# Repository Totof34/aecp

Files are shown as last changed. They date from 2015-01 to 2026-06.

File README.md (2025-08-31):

aecp
====

The project describes a electronic mapped car ignition
especialy for Panhard two cylindre

If you would have more information about this project please visit 
www.audiyofan.org

A link to the dedicated post 
http://www.audiyofan.org/forum/viewtopic.php?f=71&t=9221

PCB & schema are designed with Kicad

**********************************
*A new version called V4 in 2025*
**********************************

The new board in 2025

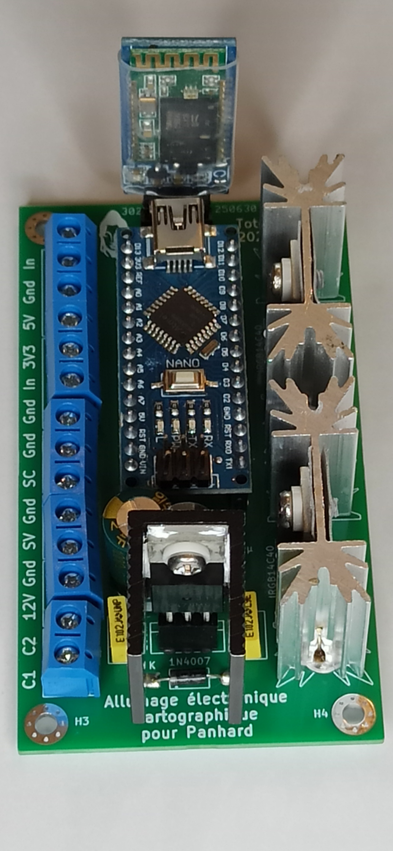
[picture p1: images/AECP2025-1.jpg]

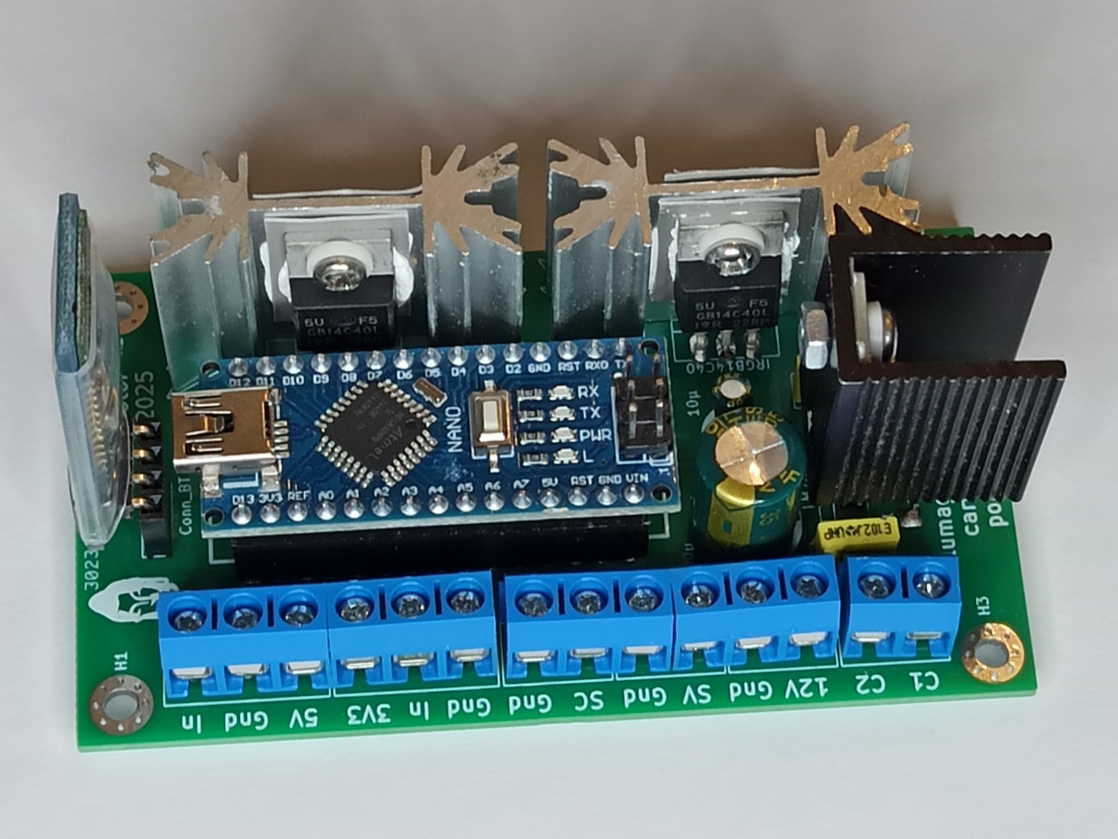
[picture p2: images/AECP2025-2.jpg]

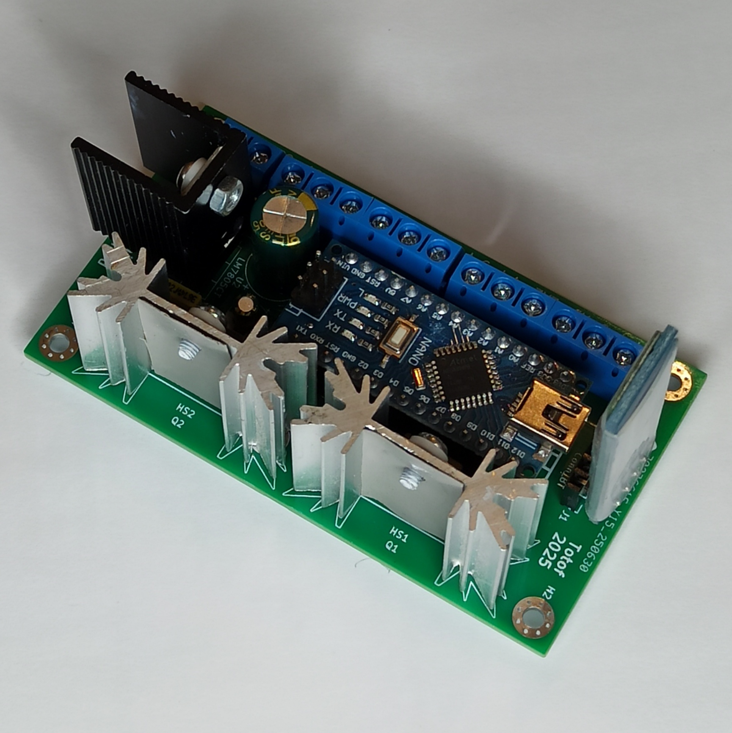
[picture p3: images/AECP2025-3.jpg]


For the Gerber's file see the folder "aecp/source_kicad/gerber V4/"

all PCB Gerber files and 3D printing files from version 2025 grouped in the folder "aecp/manufacturing_files"

*******************************************************************

the new board uses a Atmega328 and usb link or a bluetooth module ( HC-05 or 06 )
to transmit some data to the PC

it's a Arduino Nano_V3

The idea comes from this site
http://a110a.free.fr/SPIP172/plan.php3

with this startpoint
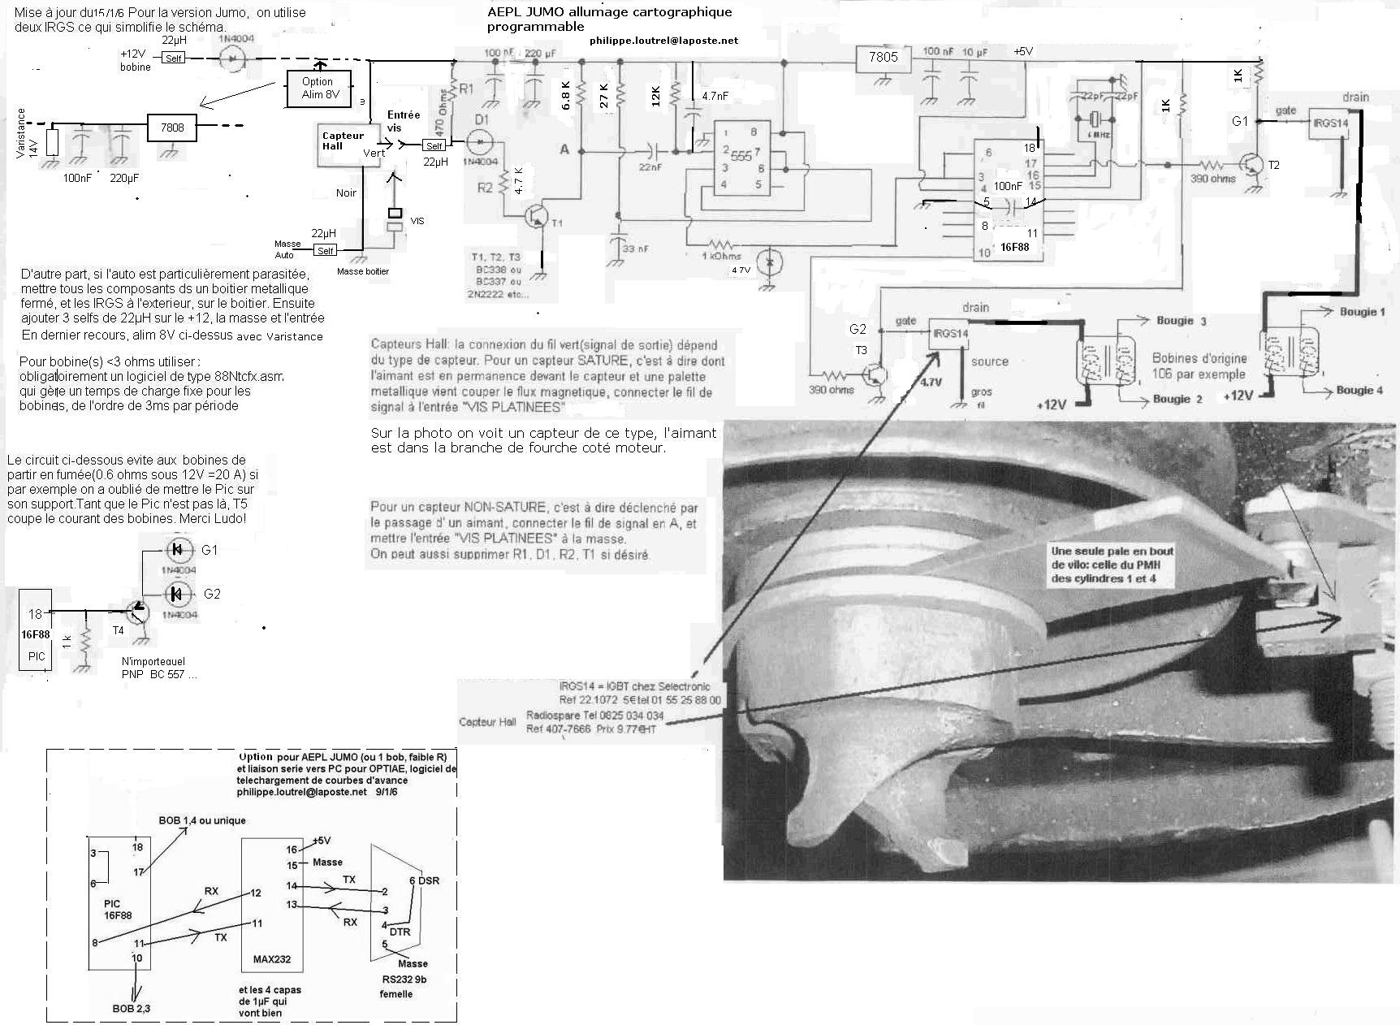
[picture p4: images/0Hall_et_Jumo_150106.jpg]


And finally with a Nano V3.0 with a dedicated page here
http://a110a.free.fr/SPIP172/article.php3?id_article=142

But this project have some child too for exemple 
https://github.com/michelm63/AEMM
with a dedicated post here
http://motos-anglaises.com/phpBB3/viewtopic.php?f=3&t=28953

All the things we need is on this picture for the hardware,
and a car of course to use it !!
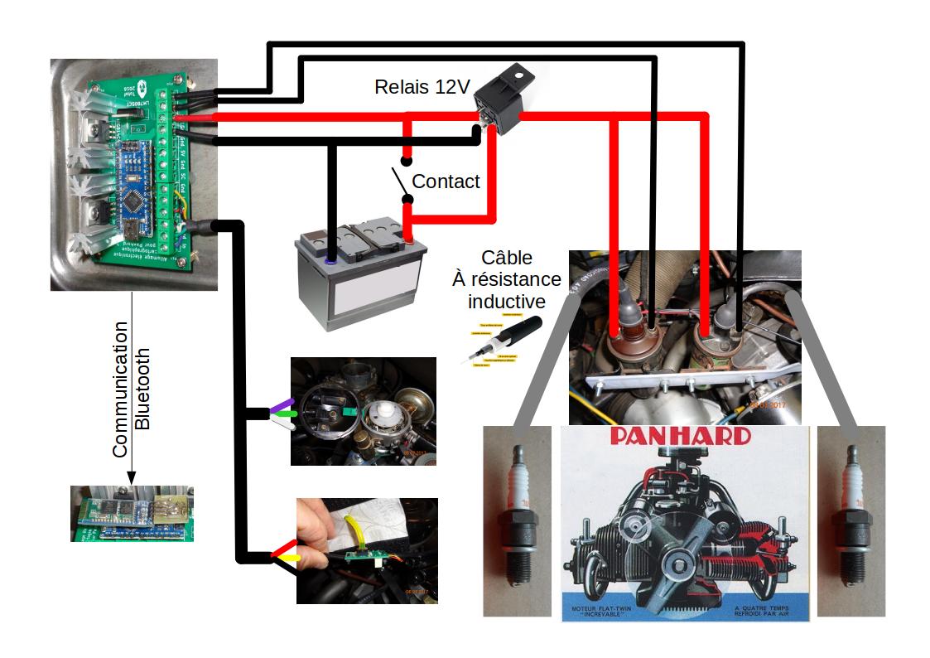
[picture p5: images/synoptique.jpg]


The prototype of the new board under construction and under kicad

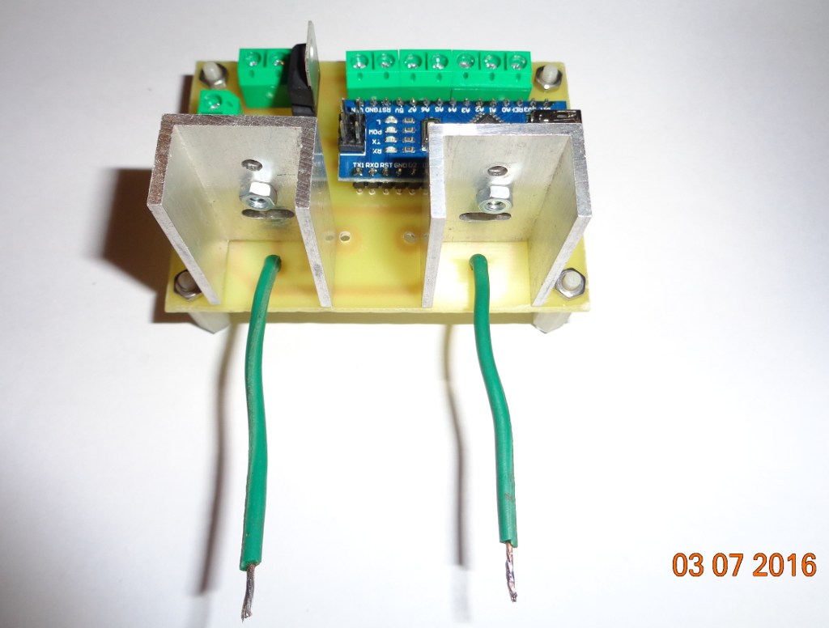
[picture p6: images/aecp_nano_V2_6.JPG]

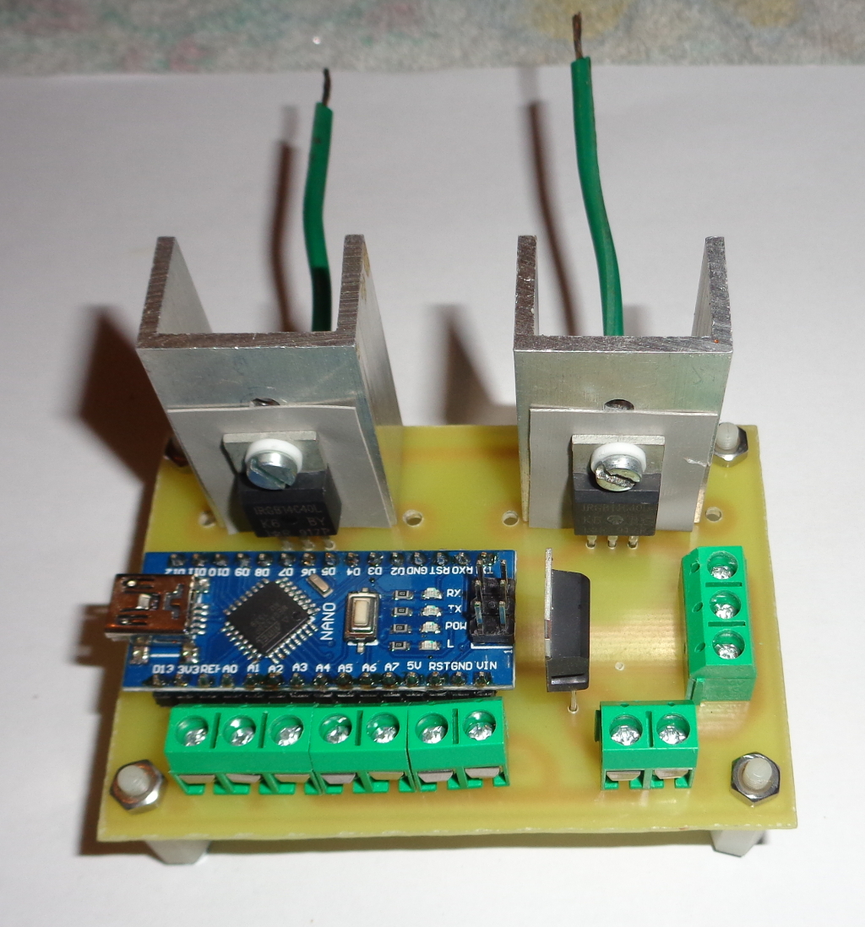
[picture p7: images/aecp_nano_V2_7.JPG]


With some parts 

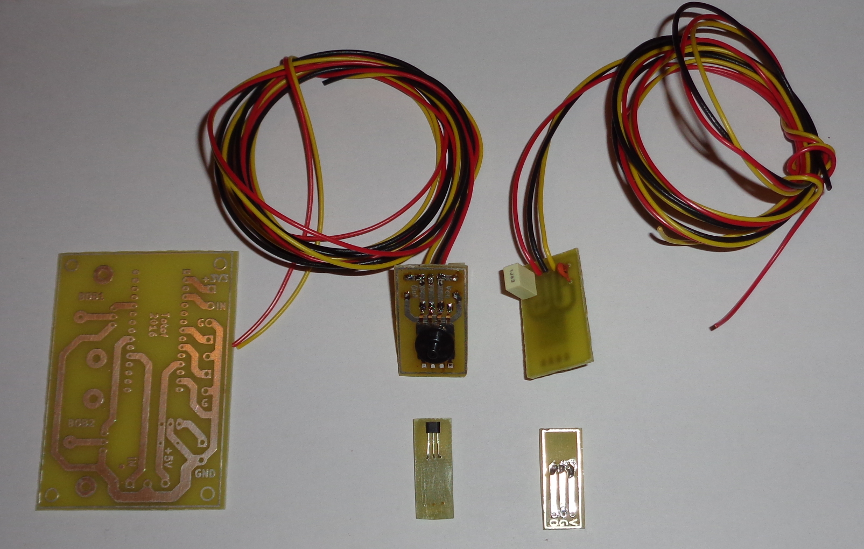
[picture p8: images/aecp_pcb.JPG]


The new version of the PCB for longtime test

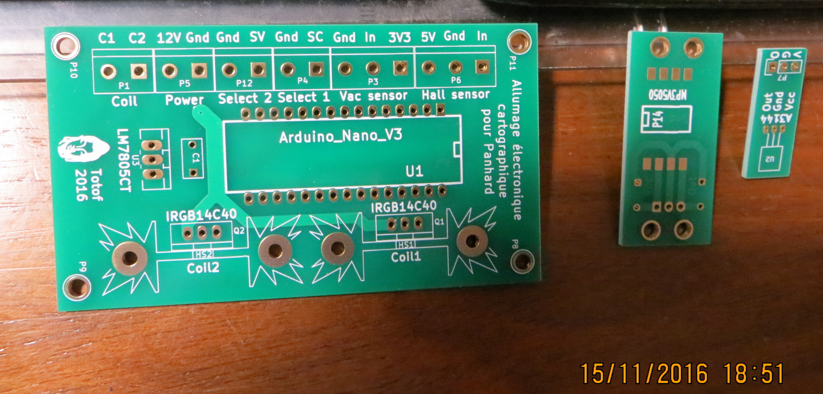
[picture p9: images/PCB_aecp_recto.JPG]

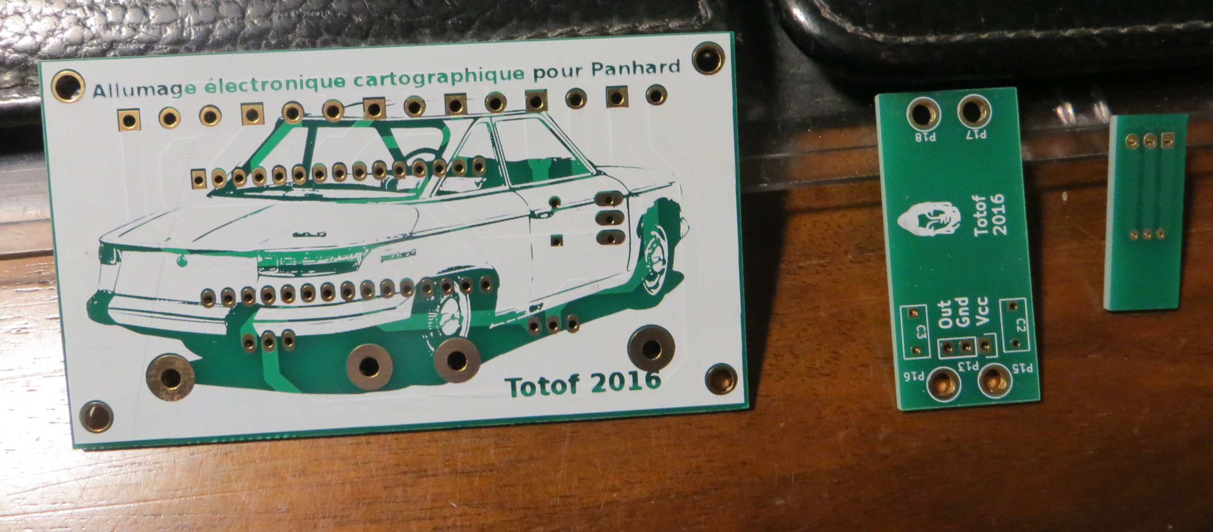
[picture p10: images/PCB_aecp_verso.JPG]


You can select different curve with a box

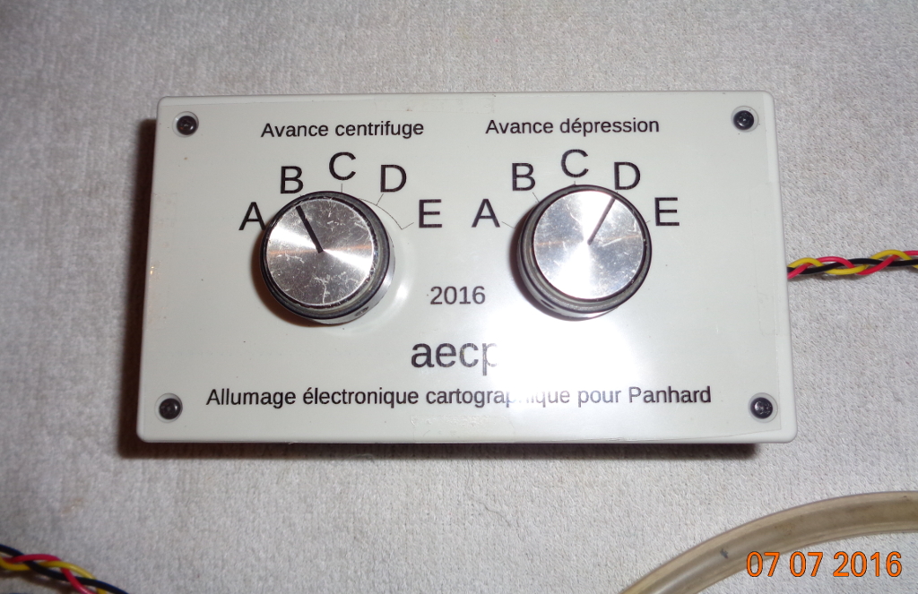
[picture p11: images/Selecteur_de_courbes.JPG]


To develop our electronic ignition, we create an new interface with a Nano_V3
to receive data from the Atmega328 and visualize the centrifugal advance curves and vacuum advance

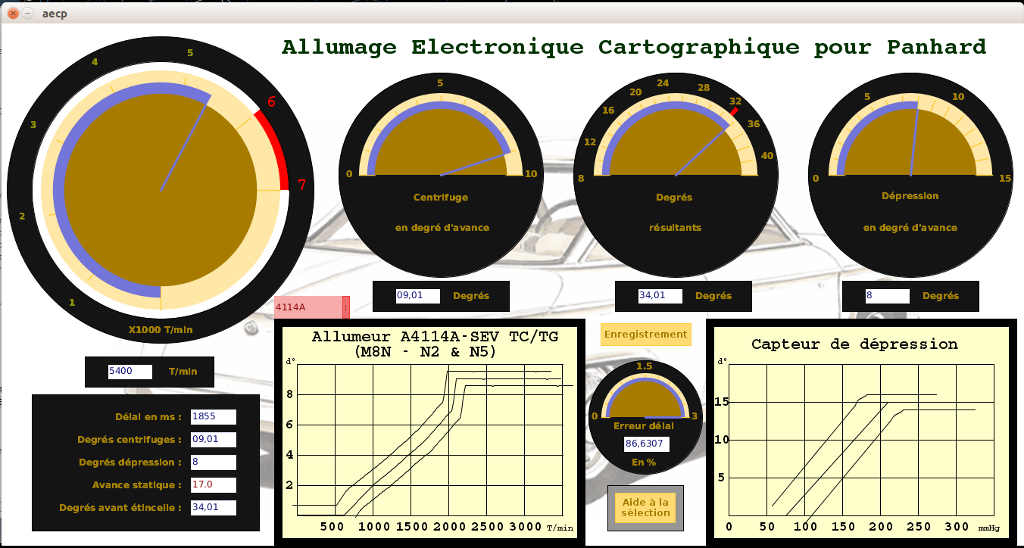
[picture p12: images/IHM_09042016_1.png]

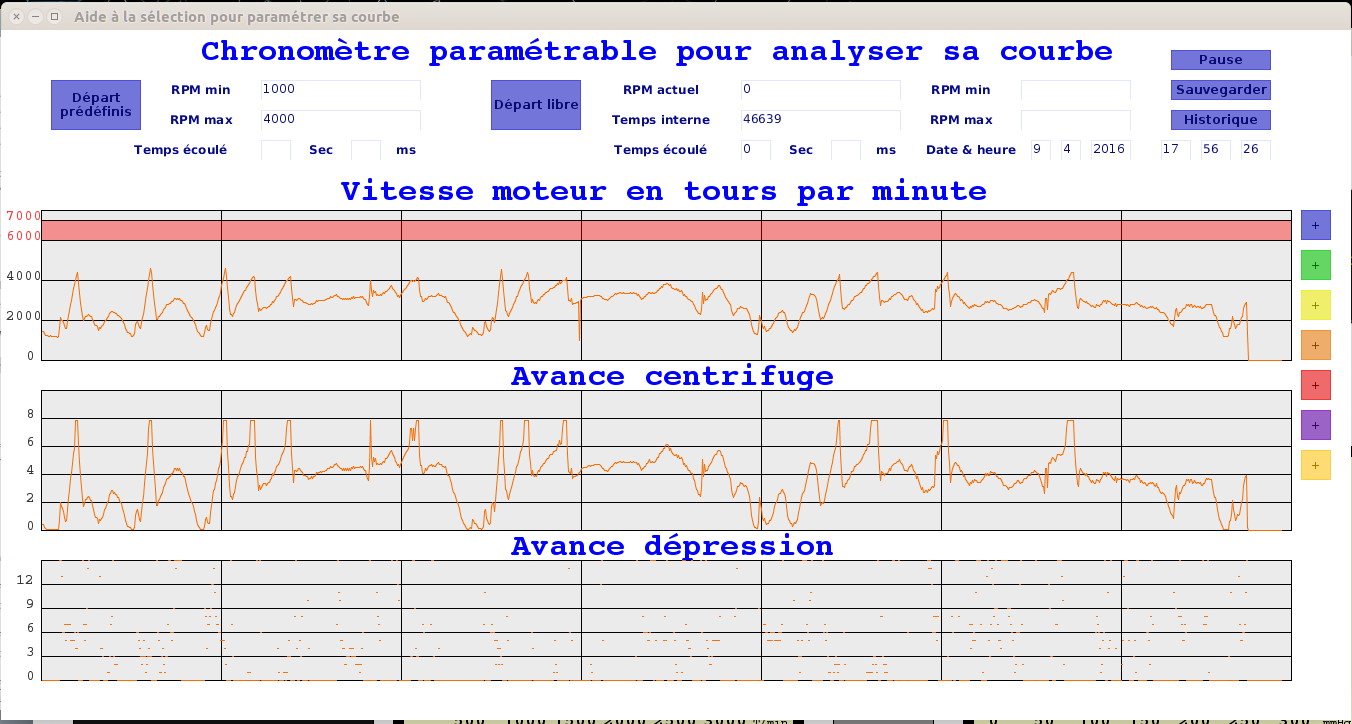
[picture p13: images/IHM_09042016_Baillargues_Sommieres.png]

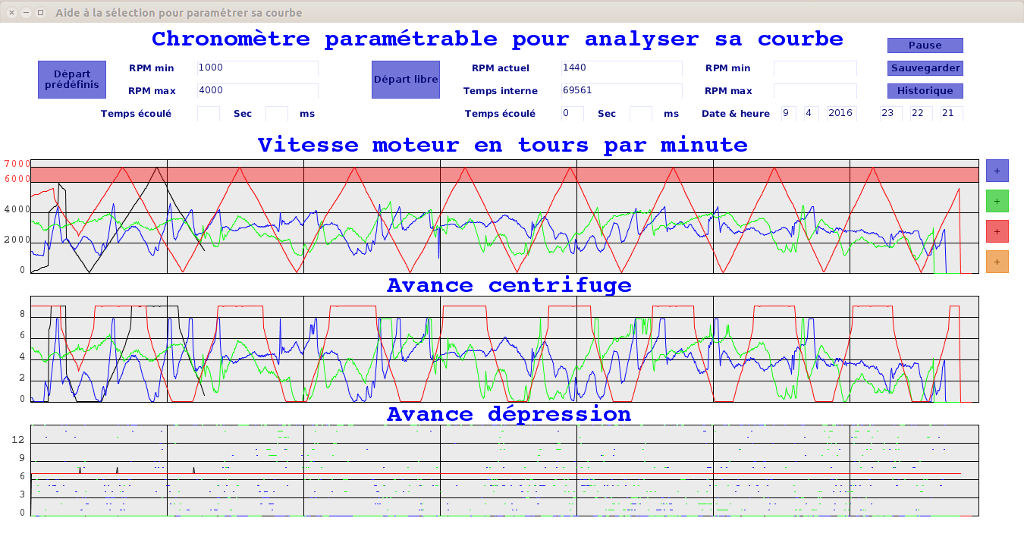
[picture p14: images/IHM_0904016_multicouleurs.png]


This interface is designed under Processing IDE and the board is programmed with Arduino IDE
All the files available in subfolders

For the printed circuit board please see the source_kicad folder 
or the build folder for a made version

For the schema see below

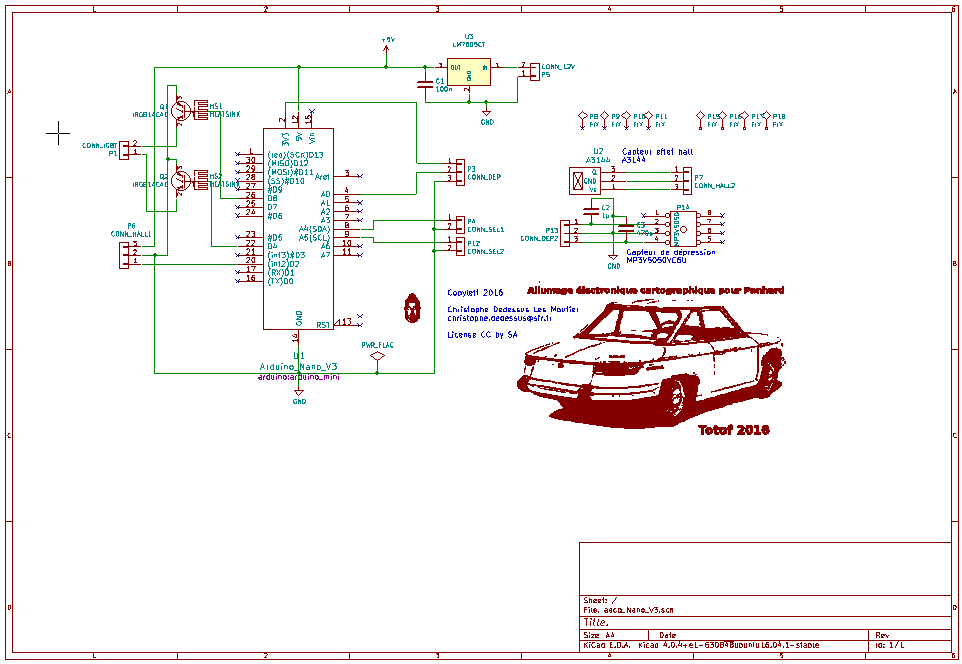
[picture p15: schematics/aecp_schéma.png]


for the rest, I suggest you to navigate into folders and open the pdf

The main code is explained through comments ( in French) in the ino file ( see Arduino folder )

Enjoy

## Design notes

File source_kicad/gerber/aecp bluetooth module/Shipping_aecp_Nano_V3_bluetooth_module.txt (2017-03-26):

aecp_Nano_V3_bluetooth_module - 26/03/2017 

Amount of Layers  : 2
PCB Thickness     : 1.6 mm
Copper Thickness  : 35 um
Plating           : Enig
Solder Mask Color : Green
Silkscreen        : Double Side
PCB Technology    : No SMD
Peel Off          : No
Electric Test     : No
Production Time   : Standard
Delivery Form     : Single PCB
PCB Dimension X   : 43.00 mm
PCB Dimension Y   : 20.00 mm
Quantity          : 20
Price per Piece   : x.xx €
Subtotal          : x.xx €

Country           : France
Shipping Method   : Registered Airmail
Payment Method    : PayPal

Votre adresse
Votre adresse
Votre adresse
Votre adresse

Phone    : +33 
Username :  
mail     :

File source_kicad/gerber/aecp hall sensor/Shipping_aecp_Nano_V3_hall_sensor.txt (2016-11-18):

aecp_Nano_V3_hall_sensor - 05/11/2016 

Amount of Layers  : 2
PCB Thickness     : 1.6 mm
Copper Thickness  : 35 um
Plating           : Enig
Solder Mask Color : Green
Silkscreen        : Double Side
PCB Technology    : No SMD
Peel Off          : No
Electric Test     : No
Production Time   : Standard
Delivery Form     : Single PCB
PCB Dimension X   : 28.00 mm
PCB Dimension Y   : 10.00 mm
Quantity          : 20
Price per Piece   : x.xx €
Subtotal          : x.xx €

Country           : France
Shipping Method   : Registered Airmail
Payment Method    : PayPal

Mr Chanteperdrix Roger
7 impasse les pêchers
34670 Baillargues
France

Phone    : +334.67.87.15.21
Username :  
mail     : chanteperdrix34@gmail.com

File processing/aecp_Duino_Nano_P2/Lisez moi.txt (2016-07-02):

Bonjour 

Cette interface peut fonctionner sous Linux mais aussi windows ou mac 
pour cela il faut adapter quelques lignes de code ou entrée dans certain fichier

La version de Processing est 2.2.1 , une migration vers Processing 3 sera possible
ultérieurement

Commencer par vérifier que vous aillez les bonne librairies d'installées ainsi que les outils
Pour la librairie c'est G4P de peter Lager 
Pour l'outil c'est G4P GUI builder de peter Lager

Ensuite il faut adapter à son OS le fichier aecp.conf
Sous Linux (comme sous mac)les chemins sont du type ci-dessous
aefmespath /home/monuser/sketchbook/myproject/aecp_Duino_Nano/aef/
AEFpath /home/monuser/sketchbook/myproject/aepl_Duino_Nano_V2/aef/PL17_pierre_baillargues_sommières.aef

Sous Windows les chemins deviennent
aefmespath C:\Users\monuser\Documents\sketchbook\myproject\aecp_Duino_Nano\aef\
AEFpath C:\Users\monuser\Documents\sketchbook\myproject\aecp_Duino_Nano\aef\mondernierfichierouvert.aef

Ce qui va aider a la fluidité d'enregistrement et recharge de l'historique ;-)

Autre différence entre linux et windows pour l'enregistrement des "data" 
il faut modifier le fichier plotutil.pde
Sous linux la fonction recordall() s'écrit comme ci-dessous
public void recordall(){
  sExportdata = ( sName + " " + day + " " + month + " " + year + " " + hour + " " + minute + " " + second);
  sData[0] = sExportdata;
  sExportdata = (speedValue + " " + correcteddelayDegree + " " + pressionValue +"\r"); // Attention version windows, enlever le "\r" car génère un CLRF
  sData[xrpmPos] = sExportdata;
  //println(sExportdata);
  //println(xrpmPos);
  //saveStrings(sName + ".aef", sData);
}
Sous windows on n'a pas besoin du caractère de fin de ligne "\r" et donc la fonction recordall() devient
public void recordall(){
  sExportdata = ( sName + " " + day + " " + month + " " + year + " " + hour + " " + minute + " " + second);
  sData[0] = sExportdata;
  sExportdata = (speedValue + " " + correcteddelayDegree + " " + pressionValue); // Attention version windows, enlever le "\r" car génère un CLRF
  sData[xrpmPos] = sExportdata;
  //println(sExportdata);
  //println(xrpmPos);
  //saveStrings(sName + ".aef", sData);
}

Je compléterai au gré des problèmes rencontrés, mon mail pour toutes questions si besoin
christophe.dedessus@sfr.fr

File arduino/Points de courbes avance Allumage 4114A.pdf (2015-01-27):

## Points de courbe "AVANCE CENTRIFUGE"

## pour Moteur M8N

Nbr de Tours Allumeur | Avance en DEGRE
550 | 0
1700 | 5
1800 | 5,5
1900 | 6,1
2000 | 6,8
2020 | 6,9
2040 | 7,1
2060 | 7,3
2080 | 7,55
2090 | 7,9
3000 | 7,9
3500 | 7,9

# Points de courbe "AVANCE DEPRESSION"

# pour Moteur M8N

Dépression en mm Hg | Avance en DEGRE
78 | 0
190 | 13,5
192 | 13,8
194 | 14,1
196 | 14,3
198 | 14,4
200 | 14,5
202 | 14,6
204 | 14,75
206 | 14,90
208 | 15,0
300 | 15,0
320 | 15,0

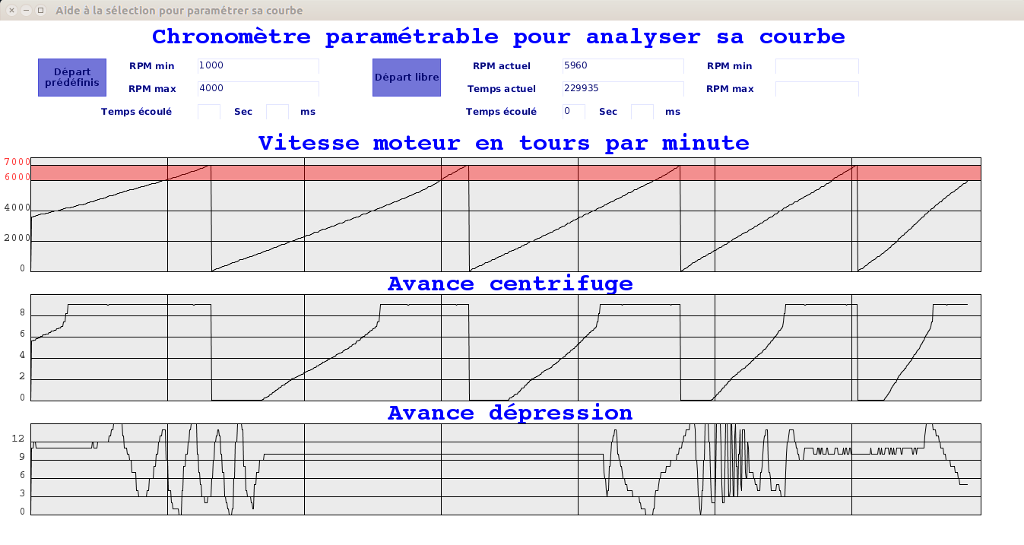
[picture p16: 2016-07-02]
images/aecp_02042016_w3.png

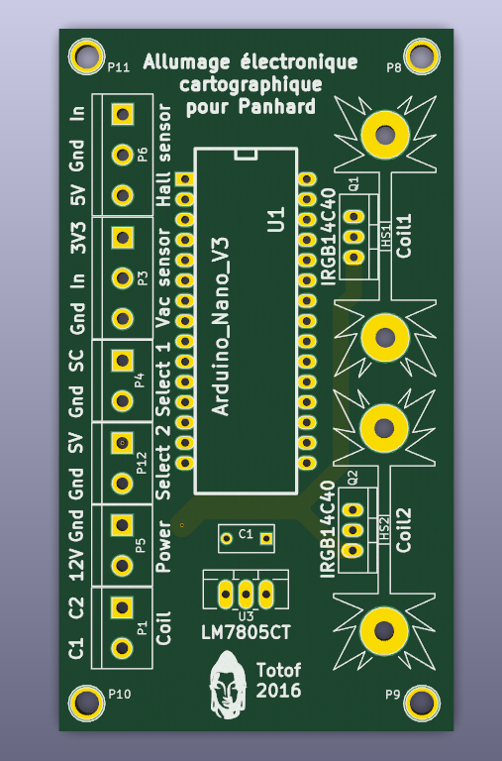
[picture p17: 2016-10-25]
images/aecp_Nano_V3_3D1.png

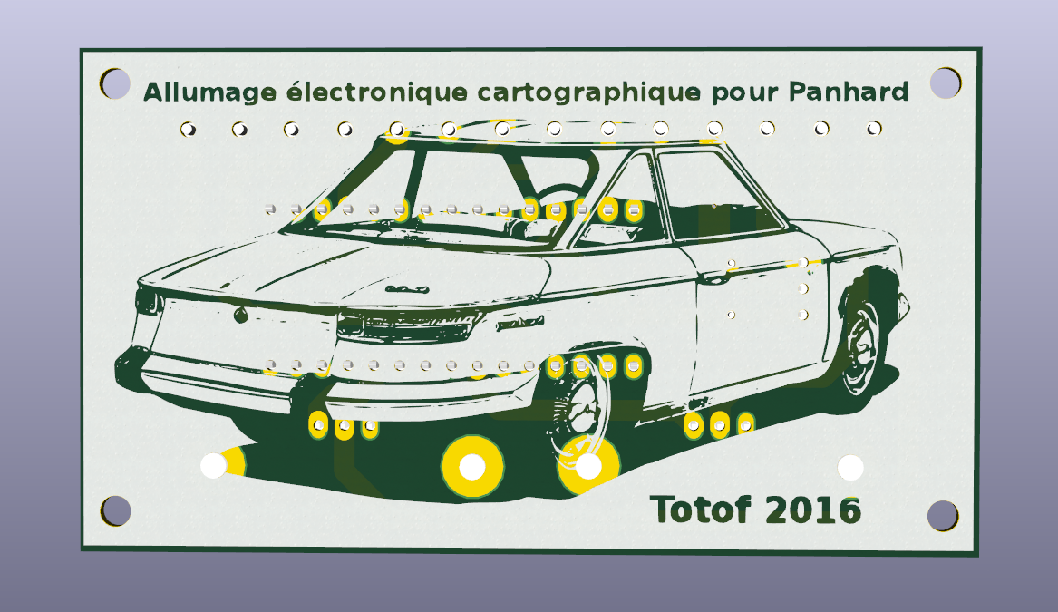
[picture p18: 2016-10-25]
images/aecp_Nano_V3_3D3.png

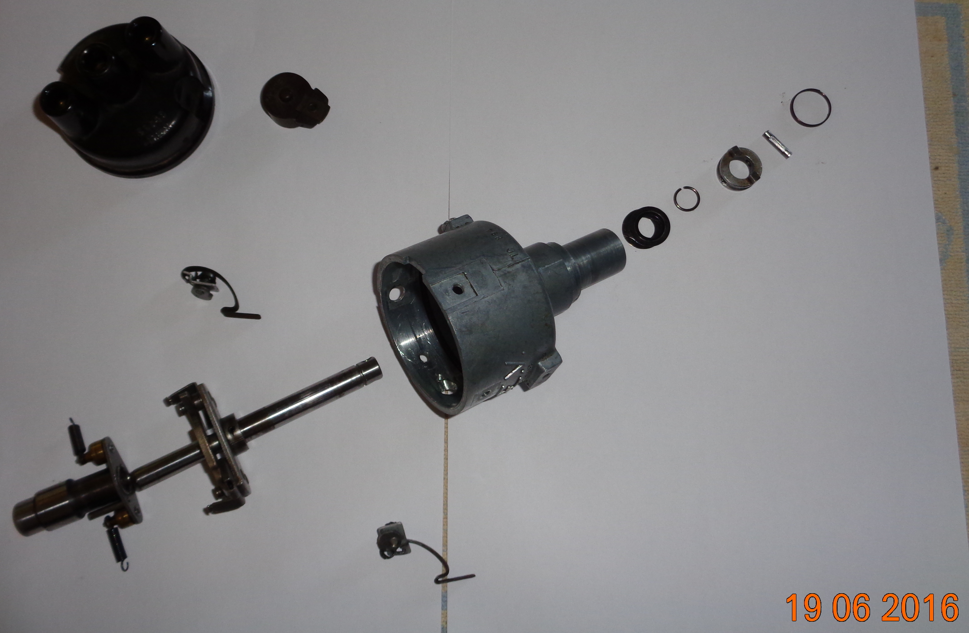
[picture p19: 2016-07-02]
images/Allumeur en pieces.JPG

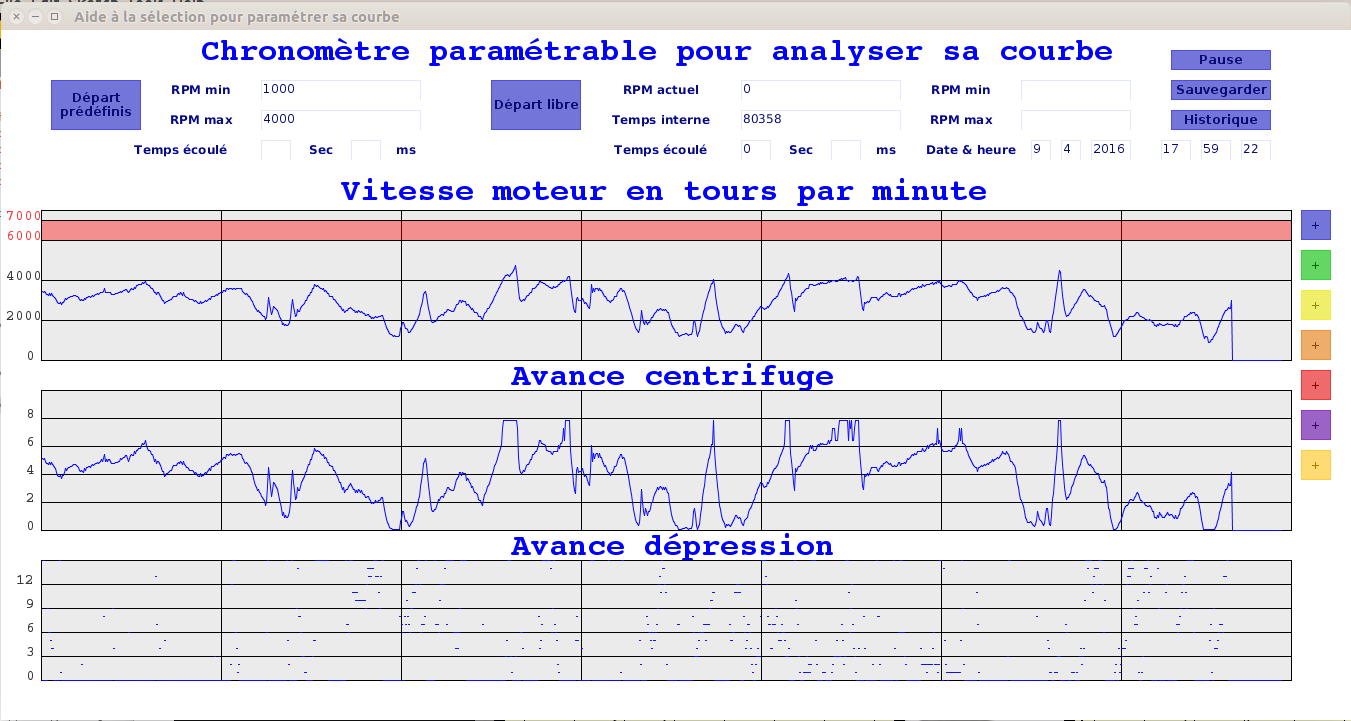
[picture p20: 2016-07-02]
images/IHM_09042106_Sommieres_Saint Drézéry.png

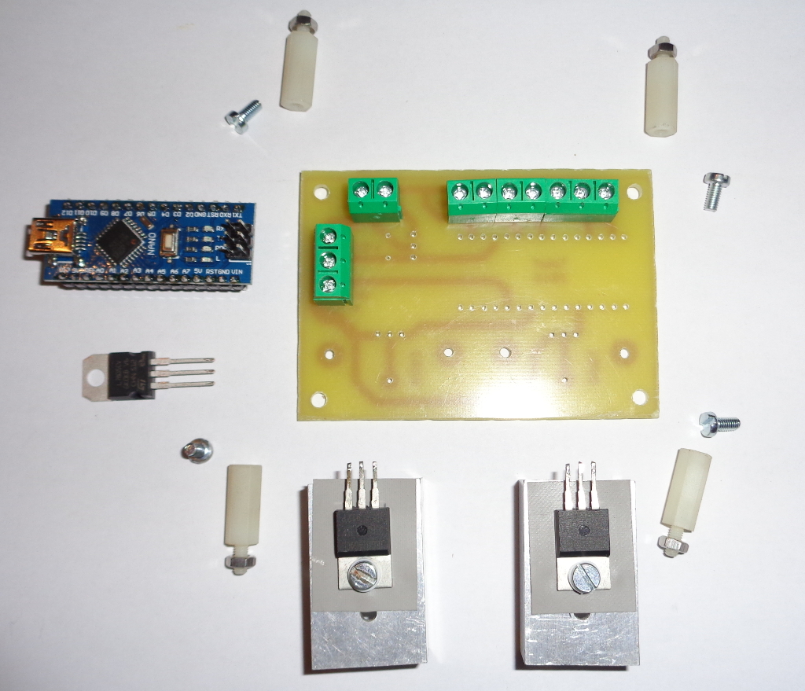
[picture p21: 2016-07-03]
images/aecp_nano_V2_3.JPG

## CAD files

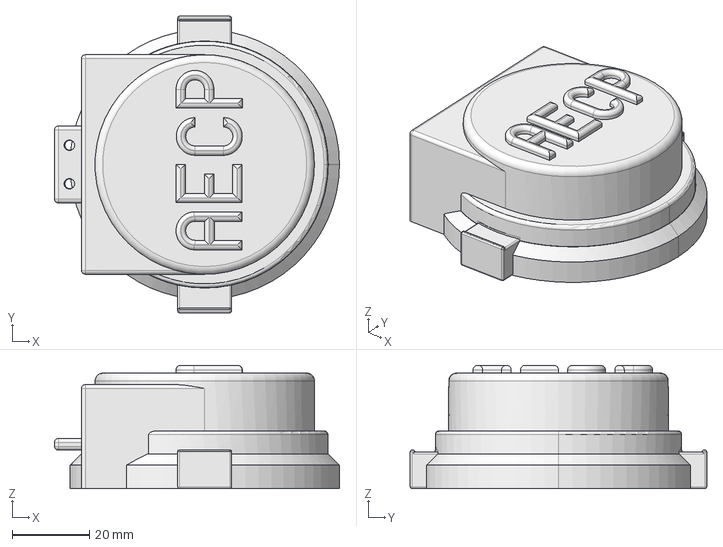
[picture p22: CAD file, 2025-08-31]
manufacturing_files/Tete delco AECP.step
74.0 x 77.0 x 32.0 mm

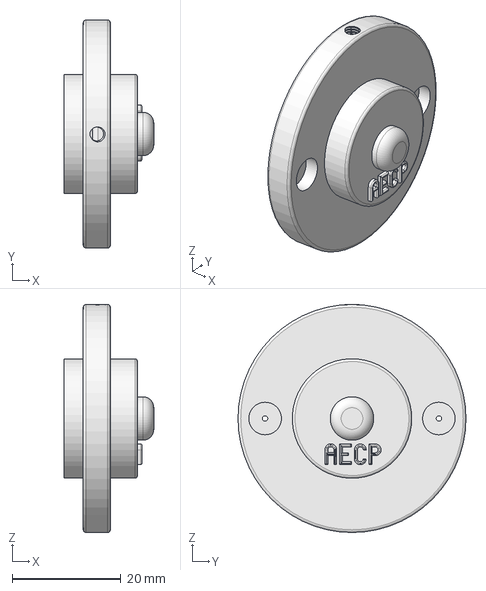
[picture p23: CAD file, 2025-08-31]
manufacturing_files/Doigt AECP.step
16.5 x 42.0 x 42.0 mm

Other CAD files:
manufacturing_files/Tete delco AECP V2.step

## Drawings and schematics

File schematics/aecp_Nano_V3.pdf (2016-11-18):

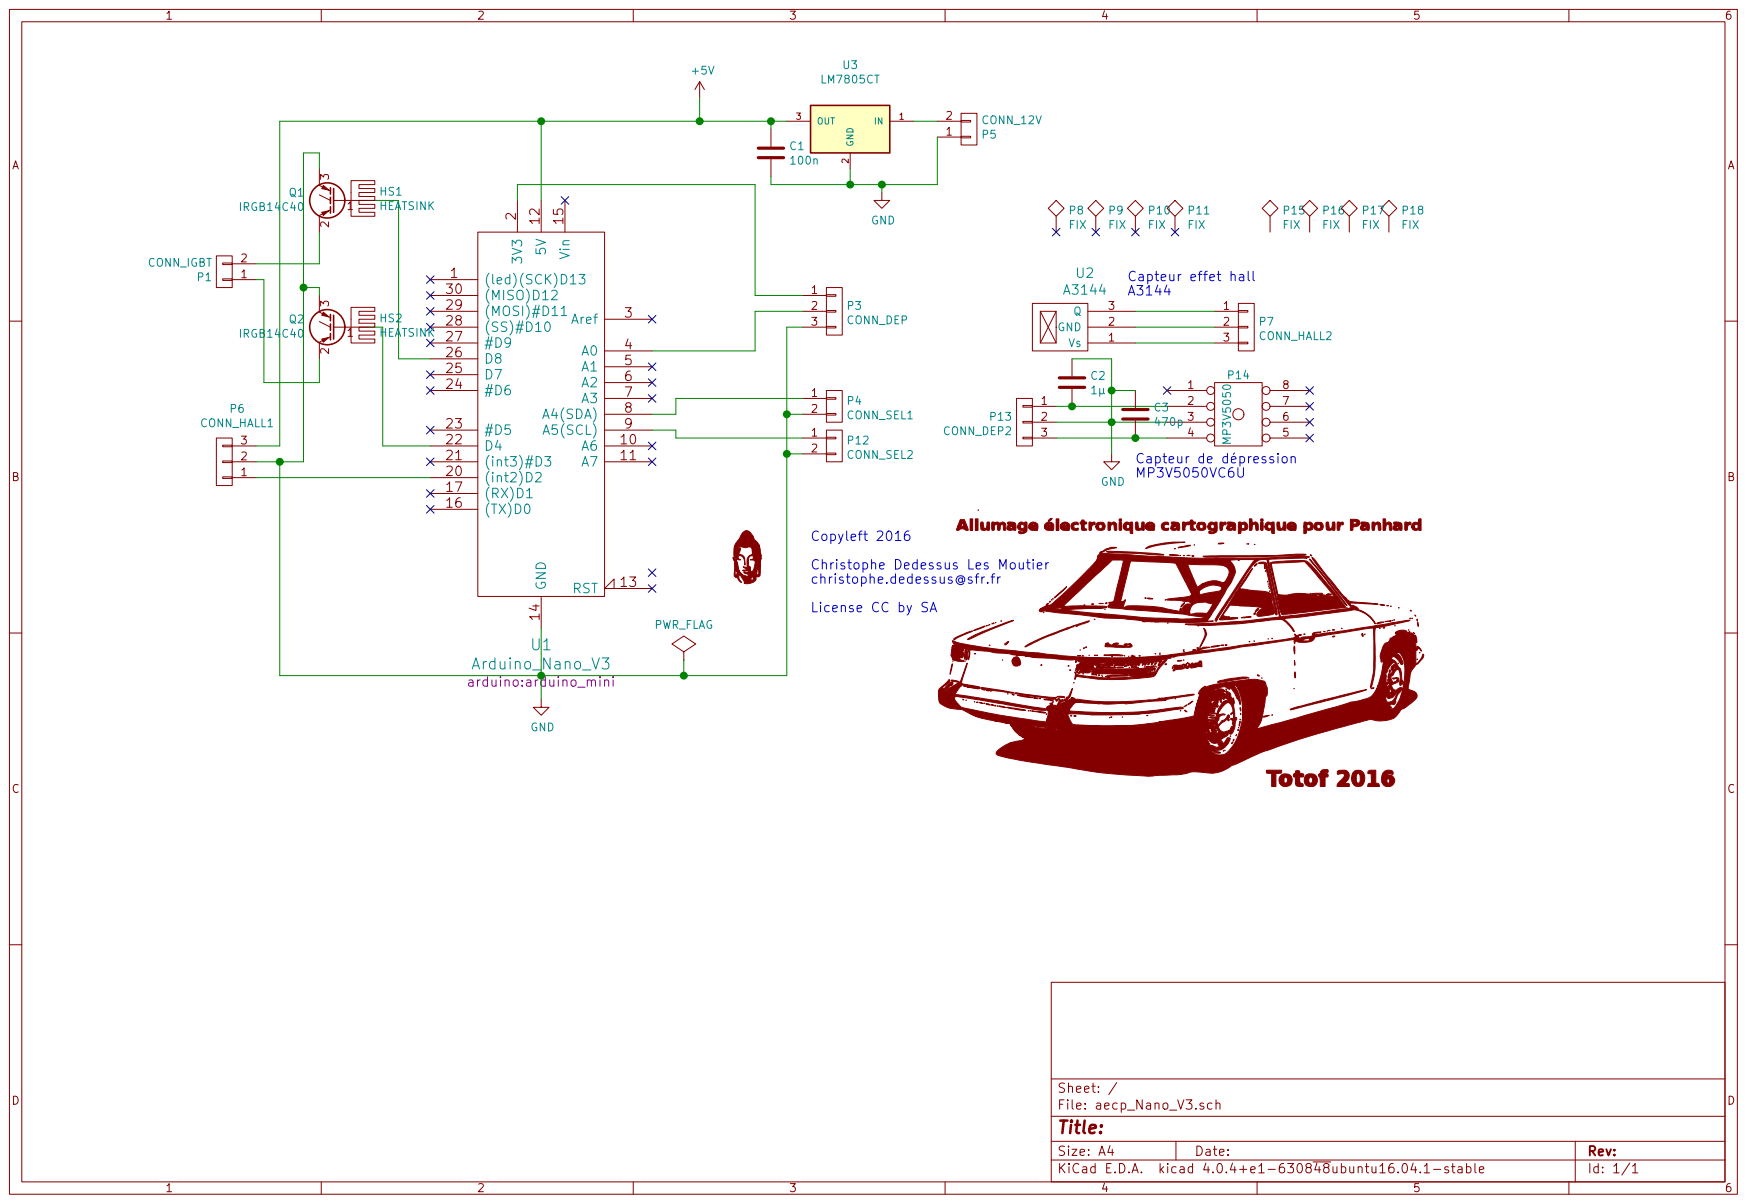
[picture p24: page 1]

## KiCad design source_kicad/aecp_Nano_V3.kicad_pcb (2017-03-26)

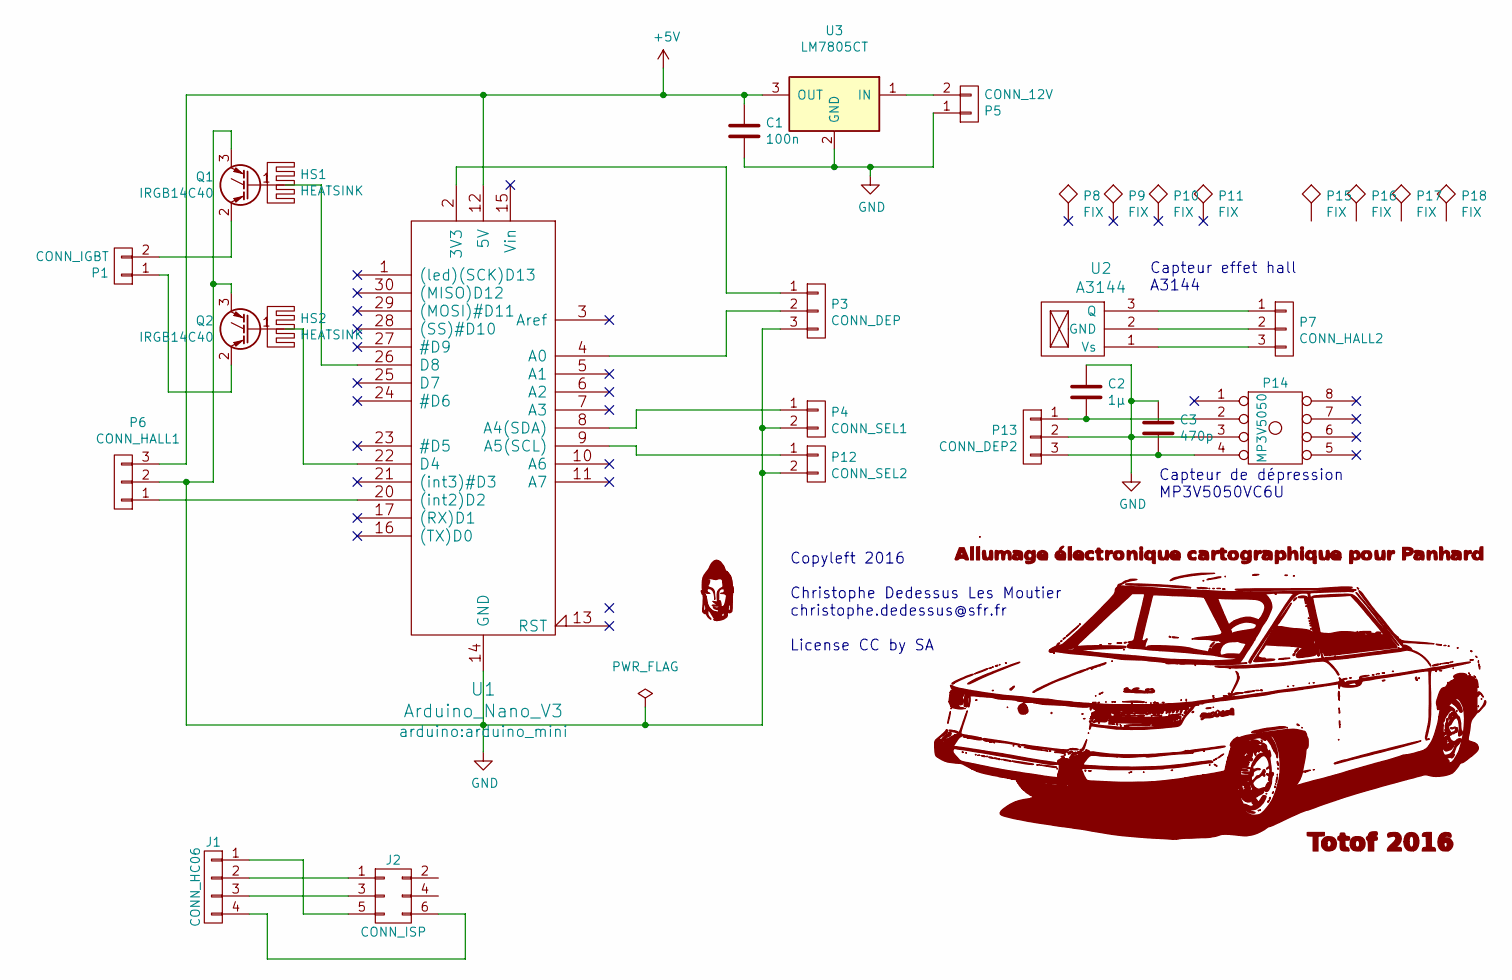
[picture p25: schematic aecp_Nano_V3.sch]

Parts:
C1: 100n; C_Rect_L7_W3.5_P5
C2: 1µ; C_Rect_L7_W3.5_P5
C3: 470p; C_Rect_L7_W3.5_P5
G1: Tete_budha
G2: 24CT; Panhard24CT
HS1, HS2: HEATSINK; Heatsink_Fischer_SK104-STC-STIC_35x13mm_2xDrill2.5mm
J1: CONN_HC06; pin_strip_4
J2: CONN_ISP; pin_strip_3x2
P1: CONN_IGBT; bornier2
P3: CONN_DEP; bornier3
P4: CONN_SEL1; bornier2
P5: CONN_12V; bornier2
P6: CONN_HALL1; bornier3
P7: CONN_HALL2; Socket_Strip_Straight_1x03
P8, P9, P10, P11: FIX; 1pin
P12: CONN_SEL2; bornier2
P13: CONN_DEP2; Socket_Strip_Straight_1x03
P14: MP3V5050; MP3V5050V
P15, P16, P17, P18: FIX; MountingHole_2.2mm_M2_Pad_Via
Q1, Q2: IRGB14C40; TO-220_Neutral123_Vertical_LargePads
U1: Arduino_Nano_V3; arduino_mini
U2: A3144; TO-92_Horizontal2_Inline_Narrow_Oval
U3: LM7805CT; TO-220_Neutral123_Vertical_LargePads

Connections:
+5V: C1.1, P6.3, U1.12 (5V), U3.3 (OUT)
GND: C1.2, C2.1, C3.1, P3.3, P4.2, P5.1, P6.2, P12.2, P13.2, P14.3, Q1.3 (E), Q2.3 (E), U1.14 (GND), U1.19 (GND), U3.2 (GND)
unnamed: C2.2, P13.1, P14.2
unnamed: C3.2, P13.3, P14.4
unnamed: J1.1, J2.5
unnamed: J1.2, J2.1
unnamed: J1.3, J2.3
unnamed: J1.4, J2.6
unnamed: P1.1, Q2.2 (C)
unnamed: P1.2, Q1.2 (C)
unnamed: P3.1, U1.2 (3V3)
unnamed: P3.2, U1.4 (A0)
unnamed: P4.1, U1.8 (A4(SDA))
unnamed: P5.2, U3.1 (IN)
unnamed: P6.1, U1.20 ((int2)D2)
unnamed: P7.1, U2.3 (Q)
unnamed: P7.2, U2.2 (GND)
unnamed: P7.3, U2.1 (Vs)
unnamed: P12.1, U1.9 (A5(SCL))
unnamed: Q1.1 (G), U1.26 (D8)
unnamed: Q2.1 (G), U1.22 (D4)

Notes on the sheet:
Copyleft 2016 Christophe Dedessus Les Moutier christophe.dedessus@sfr.fr License CC by SA
Capteur de dépression MP3V5050VC6U
Capteur effet hall A3144

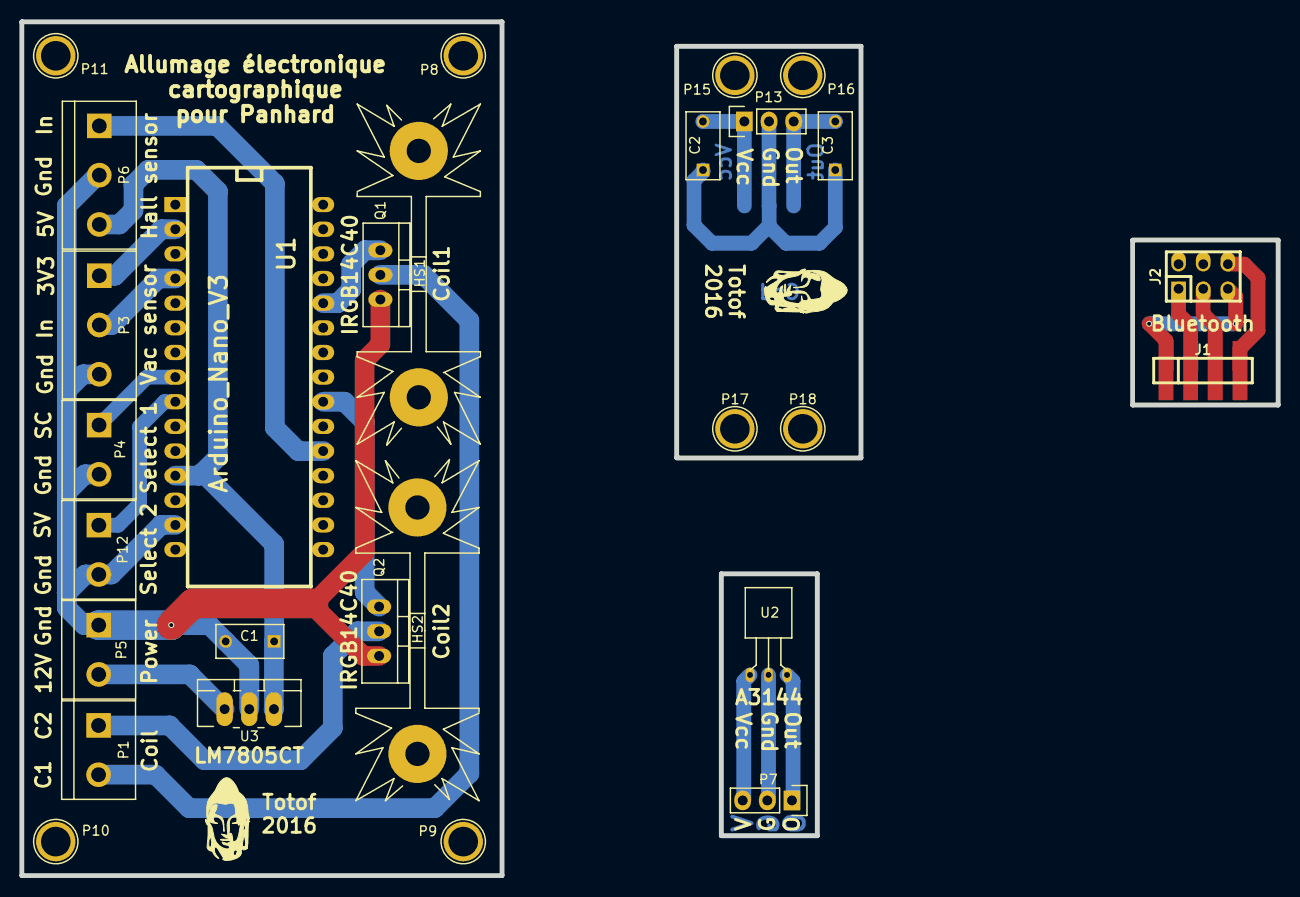
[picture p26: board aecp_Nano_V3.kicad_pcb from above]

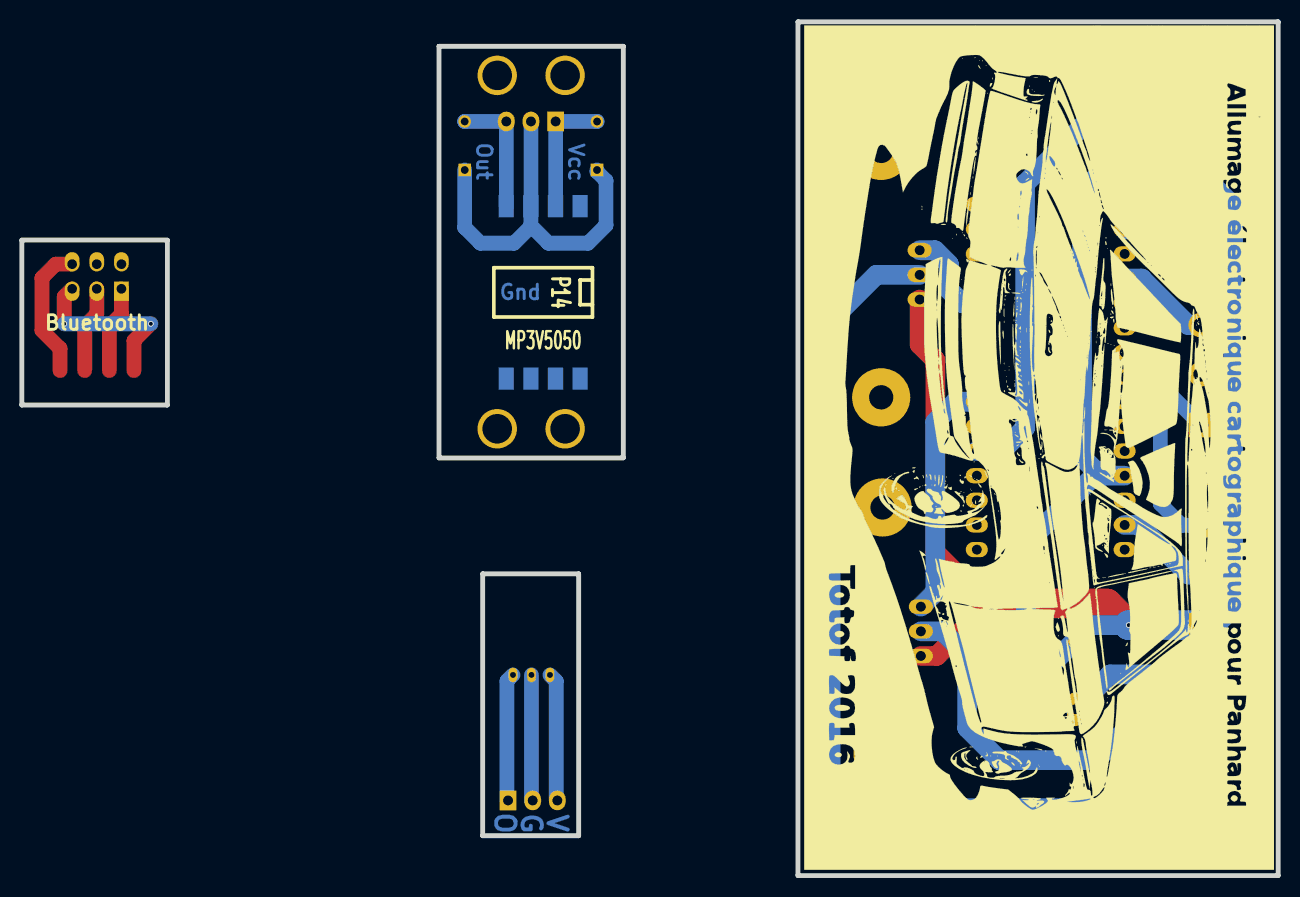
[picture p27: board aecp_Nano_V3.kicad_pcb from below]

Board: 2 copper layers, 129.5 x 88.0 mm, 32 parts (2 on the bottom side), 21 nets.

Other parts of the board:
G1#2: Tete_budha

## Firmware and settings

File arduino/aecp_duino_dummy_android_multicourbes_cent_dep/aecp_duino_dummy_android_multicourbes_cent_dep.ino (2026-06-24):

#include <TimerOne.h> //Génère une interruption toutes les  trech ou Dsecu µs
#include <SoftwareSerial.h>
//**************************************************************
//Aecp-Duino    Allumage electronique programmable - Arduino - 2016
//Mr Loutrel Philippe, voir son site,
//http://www.loutrel.org/aeduino.php
//Mr Dedessus Les Moutier Christophe pour la version Panhard
char ver[] = "version du 01_07_2020";//Choix entre 3 types de Dwell.
//En option, connexion d'un sélecteur entre la patte A4 et A5 et la masse
//pour changer de courbe d'avance centrifuge et dépression
//Les datas envoyées pour Processing sont en fin de boucle loop 
//T>14ms, correction Christophe.Avance 0°jusqu'a 500t/mn, anti retour de kick
//Detection et traitement special au demarrage (première etincelle)
//******************************************************************************
//Le module BlueTooth est le très courant HC 06 à moins de 5€
//Connecter la patte TX du module à D11, la patte RX du module à D12
//Connecter les masses et le Vcc du module au +5V du 7805 
//Mettre le module BlueTooth en mode AT( pin 34 au +5V ) et entrer AT+UART=38400,1,0
//38400 bps entre module et smartphone
//Installer l'appli BlueTerm , connecter: sur l'ecran l'avance enn degrés est affichée

SoftwareSerial BT(11, 12); // RX| TX vers le module BlueTooth HC05/06

//************* ces lignes explique la lecture de la dépression ****************
// Pour la dépression ci-dessous le tableau des mesures relevés sur un banc Souriau
// Degdep = map((analogRead(A0)),xhigh,xlow,yhigh,ylow);
int xhigh = 0;// valeur ADC haute pour conversion de la valeur mmHg haute
int xlow = 0;// valeur ADC basse pour conversion de la valeur mmHg basse
int yhigh = 0;// valeur de la limite en degré haute x 10 pour avoir les centièmes
int ylow = 0;// valeur de la limite en degré basse soit 0 degré
// tableau des valeurs mmHg vs 8 bits
// {0,707}{25,667}{50,620}{60,601}{75,576}{80,565}{95,538}{100,530}{125,485}{150,438}{175,394}{185,373}{200,350}{210,330}{225,305}{250,260}{275,216}{300,172}
// relevé en activant la ligne Degdepcal et en ajoutant cette variable à l'édition dans le terminal série
// on peut en déduire une équation qui donne la valeur en mmHg au départ de la conversion ADC , utilisé sous Processing
// mmHg = (707 - valeur ADC)/1.78 ou 1.78 est la pente du capteur pour tension VS mmHg

//**************  Ces 6 lignes sont à renseigner obligatoirement.****************
// Ce sont : Na[],Anga[],  Ncyl, AngleCapteur, CaptOn, Dwell
//Les tableau Na[] et Anga[] doivent obligatoirement débuter puis se terminer par  0
//et  contenir des valeurs  entières >=1
//Le nombre de points est libre.L'avance est imposée à 0° entre 0 et Nplancher t/mn
//Le dernier N fixe la ligne rouge, c'est à dire la coupure de l'allumage
int Na[] = {0,1240,2050,2500,3400,4100,4200,7000, 0};
//degrés d'avance vilebrequin correspondant soit en tour volant moteur ( attention ! ):
int Anga[] = {0,0,4,6,10,14,16,16, 0};

int arrayVitesse[] = {1440,1320,1360,1240,1240,1240,1200,1200,1240,1160,1200,1200,1160,1200,1200,1120,1200,1640,2120,2000,1960,1880,1720,1560,1600,1920,2240,2480,
2800,2960,3280,3600,3760,4000,4240,4360,3840,3320,2840,2520,2200,2000,2080,2200,2200,2240,2280,2240,2160,2160,2040,1920,1800,1720,1720,1680,1480,1640,1600,1680,1720,
1800,1920,1960,2040,2120,2160,2320,2360,2440,2440,2360,2400,2320,2320,2240,2240,2160,2120,2080,1960,1880,1760,1600,1480,1360,1360,1320,1320,1200,1160,1240,1320,1760,
1880,1920,1800,1640,1560,1880,2120,2280,2640,3260,3820,4240,4960,5580,6160,6260,5760,5280,4840,3480,2840,2040,2160,2200,2280,2320,2400,2520,2600,2640,2760,2800,2800,
2840,2840,2920,2920,3000,3080,3080,3040,3080,3040,3080,3000,2960,2920,2840,2840,2720,2600,2480,2360,2280,2200,2120,2080,2000,1880,1800,1600,0};
float arrayDep[] = {0,0,0,0,0,0,0,0,0,0,0,0,0,0,0,0,0,15,15,13,6,6,7,5,7,7,7,7,5,5,5,5,6,4,4,6,0,0,0,0,15,7,5,7,9,14,15,0,0,0,0,0,0,0,0,0,0,13,4,4,3,0,0,0,0,1,1,3,7,
8,15,3,2,2,2,0,0,0,0,0,0,0,0,0,0,0,0,0,0,0,0,0,0,0,6,6,5,4,3,2,3,5,3,1,2,3,4,3,3,0,0,0,0,0,15,6,5,1,1,3,4,2,1,3,3,7,15,15,6,5,6,9,15,14,15,15,15,15,15,0,0,0,0,0,0,0,
0,0,0,0,0,0,0,0,0,0};

int Ncyl = 2;           //Nombre de cylindres, moteur Panhard
const int AngleCapteur = 90; //le capteur(Hall) est 45° avant le PMH habituellement
const int Avancestatique = 17; // Correspond à 5 dents d'avance statique sur volant moteur
const int CaptOn = 0;  //CapteurOn = 1 déclenche sur front montant (capteur saturé)
//CapteurOn = 0 déclenche sur front descendant (capteur non saturé).Voir fin du listing
//**********************************************************************************
const int Dwell = 1; //1 pour alimenter la bobine en permanence sauf 1ms/cycle.Elle doit pouvoir chauffer sans crainte
// 2 pour alimentation de la bobine seulement trech ms par cycle, 3ms par exemple,
//indispensable pour bobine 'electronique' ou  de faible resistance: entre 2 et 0.5ohm
//3 pour simuler un allumage à vis platinées: bobine alimentée 2/3 (66%) du cycle.
//************************************************************************************
//*******************MULTICOURBES****IL FAUT TOURNER LE SELECTEUR!!!!!!!*******
//A la place de la courbe a, on peut selectionner la courbe b, c, d ou la e
//Un sélecteur rotatif et 4 résistances de 4K7, 18K, 47K et 100K font le job
//avec l'entrée configurée en Input Pull-up
//*******//*********Courbe   b
int Nb[] = {0, 1640, 2000, 2480, 3800, 4000, 4120,4240, 4360, 7000, 0}; //Courbe b 
int Angb[] = {0, 0, 2, 4, 10, 11, 12, 13, 14, 14, 0};
//*******//*********Courbe   c
int Nc[] = {0,840, 2100, 3000, 3400, 3760, 3880, 3950, 4000, 7000, 0}; //Courbe c
int Angc[] = {0, 0, 6, 10, 12, 14, 15, 16, 18, 18, 0};
//*******//*********Courbe   d
int Nd[] = {0, 1640, 2520, 2840, 3760, 3880, 3990, 4000, 7000, 0}; //Courbe d
int Angd[] = {0, 0, 5, 7, 14, 15, 16, 18, 18, 0};
//*******//*********Courbe   e
int Ne[] = {0, 840, 2000, 2580, 3520, 3800, 4000, 4120, 4240, 4360, 7000, 0}; //Courbe e
int Ange[] = {0, 0, 4, 6, 9, 10, 11, 12, 13, 14, 14, 0};
//**********************************************************************************
//************Ces 4 valeurs sont eventuellement modifiables*****************
//Ce sont Nplancher, trech , Dsecu et delAv
const int Nplancher = 500; // vitesse en t/mn jusqu'a laquelle l'avance  = 0°
const int trech  = 3000;//temps de recharge bobine, 3ms= 3000µs typique
const int unsigned long Dsecu  = 1000000;//Securite: bobine coupee à l'arret apres Dsecu µs
int delAv = 1;//delta avance,par ex 2°. Quand Pot avance d'une position, l'avance croit de delAv

const int Bob1 = 8;    //Sortie D8 vers bobine1
const int Bob2 = 4;    //Sortie D4 vers bobine2
const int Cible = 2;  //Entrée sur D2 du capteur, R PullUp et interrupt
const int Pot1 = A4;   //Entrée analogique sur A4 pour potard de changement de courbes. R PullUp
const int Pot2 = A5;   //Entrée analogique sur A5 pour potard de changement de courbes d'avance dépression. R PullUp
const int Led = 13; //Sortie D13 avec la led built-in pour caller le disque par rapport au capteur 
int unsigned long D = 0;  //Delai en µs à attendre après la cible pour l'étincelle
int unsigned long Ddep = 0;
int unsigned long Dsum = 0;
int valPot1 = 0;       //0 à 1023 selon la position du potentiomètre en entree
int valPot2 = 0;       //0 à 1023 selon la position du potentiomètre en entree
int milli_delay = 0;
int micro_delay = 0;
float RDzero = 0; //pour calcul delai avance 0° < vitesse seuil plancher
float  Tplancher = 0; //idem
const int tcor  = 380; //correction en µs  du temps de calcul pour D 120µs + 120µs de lecture de dépression + 140µs de traitement
int unsigned long Davant_rech = 0;  //Delai en µs après etincelle pour demarrer la recharge bobine.
int unsigned long Tprec  = 0;//Periode precedant la T en cours, pour calcul de Drech
int unsigned long prec_H  = 0;  //Heure du front precedent en µs
int unsigned long T  = 0;  //Periode en cours
int N1  = 0;  //Couple N,A de debut d'un segment
int Ang1  = 0; // Car A1 reservé pour entrée analogique!
int N2  = 0; //Couple N,A de fin de segment
int Ang2  = 0;
int*  pN = &Na[0];//pointeur au tableau des régimes. Na sera la courbe par defaut
int*  pA = &Anga[0];//pointeur au tableau des avances. Anga sera la  courbe par defaut
float k = 0;//Constante pour calcul de l'avance courante
float C1[20]; //Tableaux des constantes de calcul de l'avance courante
float C2[20]; //Tableaux des constantes de calcul de l'avance courante
float Tc[20]; //Tableau des Ti correspondants au Ni
//Si necessaire, augmenter ces 3 valeurs:Ex C1[30],C2[30],Tc[30]
int Tlim  = 0;  //Période minimale, limite, pour la ligne rouge
int j_lim = 0;  //index maxi des N , donc aussi  Ang
int unsigned long NT  = 0;//Facteur de conversion entre N et T à Ncyl donné
int AngleCibles = 0;//Angle entre 2 cibles, 180° pour 4 cyl, 120° pour 6 cyl, par exemple
int UneEtin = 1; //=1 pour chaque étincelle, testé par isr_CoupeI et remis à zero
int Ndem = 60;//Vitesse estimée du vilo entrainé par le demarreur en t/mn
int unsigned long Tdem  = 0;  //Periode correspondante à Ndem,forcée pour le premier tour
int Mot_OFF = 0;//Sera 1 si moteur detecté arrété par l'isr_GestionIbob()
int Vitesse = 0; //Vitesse de rotation moteur
float   AV = 0; //Avance en degrès pour transmission vers module BlueTooth
float   AVtot = 0; //Avance totale en degrés pour transmission vers module BlueTooth
String Message = ""; //Données renvoyer au smartphone ou pc via bluetooth ou usb

float uspardegre = 0;
int Dep = 0;
float Degdep = 0;

float Delaideg  = 0;  //µs/deg pour la dépression
// Tableau pour sauver des données temporelle
unsigned long Stop_temps;
unsigned long Tempsecoule = 0;

char  carLu;//Sera utilisé pour changer de courbe

// Define various ADC prescaler
const unsigned char PS_16 = (1 << ADPS2);
const unsigned char PS_32 = (1 << ADPS2) | (1 << ADPS0);
const unsigned char PS_64 = (1 << ADPS2) | (1 << ADPS1);
const unsigned char PS_128 = (1 << ADPS2) | (1 << ADPS1) | (1 << ADPS0);

//Macro  ps(v) de debug pour imprimer le numero de ligne, le nom d'une variable, sa valeur
//puis s'arreter definitivement .
#define ps(v) Serial.print("Ligne_") ; Serial.print(__LINE__) ; Serial.print(#v) ; Serial.print(" = ") ;Serial.println((v)) ; Serial.println("  Sketch stop"); while (1);
//Exemple, à la ligne 140, l'instruction     ps(var1);
//inprimera  "Ligne_140var1 = 18  Sketch stop"

//Macro  pc(v)de debug pour imprimer le numero de ligne, le nom d'une variable, sa valeur,
//puis s'arreter et attendre un clic de souris  sur le bouton 'Envoyer'en haut de l'ecran seriel pour continuer.
#define pc(v) Serial.print("Ligne_") ; Serial.print(__LINE__) ; Serial.print(#v) ;Serial.print(" = ") ; Serial.println((v)) ; Serial.println(" Clic bouton 'Envoyer' pour continuer") ;while (Serial.available()==0);{ int k_ = Serial.parseInt() ;}
//Exemple, à la ligne 145, l'instruction    pc(var2);
// inprimera   "Ligne_145var2 = 25.3   Clic bouton 'Envoyer' pour continuer"

int deb = 0; //0 sinon 1 ou 2 pour le debugging,et executer les impressions pc() ou pc(). Voir Setup()

//********************LES FONCTIONS*************************

void  CalcD ()////////////////////while (1); delay(1000);/////////////////////////////
// Noter que T1>T2>T3...
{ for (byte j = 1; j <= j_lim; j++)//On commence par T la plus longue et on remonte
  { //Serial.print("Tc = "); Serial.println(Tc[j]);delay(1000);
    if  (T >=  Tc[j]) {     //on a trouvé le bon segment de la courbe d'avance
      D = float(T * C1[j]  + C2[j]);//D en µs, C2 est déjà diminué du temps de calcul~50mus
      if ( T > Tplancher)D = T * RDzero;
      //break;  //Sortir, on a D
      Ddep = (Degdep * Delaideg ) ;//Ddep en µs
      Dsum = D - Ddep - tcor ;// tcor appliqué ici donne de meilleurs résultats niveau précision
      //if (deb > 1) {  pc(C1[j] );  pc(C2[j] );pc(D);}
      break;
    }
  }
}
void  Etincelle ()//////////while (1); delay(1000);/////////////////////////////
//{gf = 1; while (gf < D/14)gf++;//10= 100µs,100=1.1ms,2000=21.8ms//attente possible
{ 
  if (Dsum < 6500){
    delayMicroseconds(Dsum);} 
  else {
  milli_delay = ((Dsum/1000)-2);  //Quand D >10ms car problèmes avec delayMicroseconds(D) si D>14ms!
  micro_delay = (Dsum-(milli_delay*1000)); // 
  delay(milli_delay); // Currently, the largest value that will produce an accurate delay is 16383 µs
  delayMicroseconds(micro_delay); 
  }
  digitalWrite(Bob1, 0); //Couper le courant, donc étincelle
  digitalWrite(Bob2, 0); //Couper le courant, donc étincelle
  Stop_temps = micros();
  switch (Dwell)  //Attente courant coupé selon le type de Dwell

  { case 1:       //Ibob coupe 1ms par cycle seulement, la bobine peut chauffer
      Davant_rech = 1000; //1ms off par cycle
      break;

    case  2:      //Type bobine faible resistance, dite "electronique"
      Davant_rech = 2 * T - Tprec - trech; //Tenir compte des variations de régime moteur
      Tprec = T;    //Maj de la future periode precedente
      break;

    case  3:      //Type "vis platinées", Off 1/3, On 2/3
      Davant_rech = T / 3;
      break;
  }
  Timer1.initialize(Davant_rech);//Attendre Drech µs avant de retablire le courant dans la bobine
  UneEtin = 1; //Signaler une étincelle à l'isr_GestionIbob().
  Change_de_Courbe();
}
void  Init ()////////////////////while (1); delay(1000);/////////////////////////////
{ AngleCibles = 720 / Ncyl; //Ex pour 4 cylindres 180°, et 120° pour 6 cylindres
  NT  = 120000000 / Ncyl; //Facteur de conversion Nt/mn en Tµs
  Tdem  = NT/Ndem;//Periode de la première étincelle
  Tplancher = 120000000 / Nplancher / Ncyl; //T à  vitesse plancher en t/mn, en dessous, avance centrifuge = 0
  RDzero = float(AngleCapteur - Avancestatique) / float(AngleCibles);
  Select_Courbe();  //Ajuster éventuellement les pointeurs pN et pA pour la courbe b ou c 
  Select_Courbe_depression(); // Sélectionne pour la courbe a,b,c,d ou e de dépression
  Prep_courbe();
  
  Serial.print("Tc = "); for (int i = 1 ; i < 8; i++)Serial.println(Tc[i]);
  Serial.print("Tlim = "); Serial.println(Tlim);
  Serial.print("C1 = "); for (int i = 1 ; i < 8; i++)Serial.println(C1[i]);
  Serial.print("C2 = "); for (int i = 1 ; i < 8; i++)Serial.println(C2[i]);

  //Timer1 a deux roles:
  //1....couper le courant dans la bobine en l'absence d'etincelle pendant plus de Dsecu µs
  //2... après une étincelle, attendre le delais Drech avant de retablir le courant dans la bobine
  //Ce courant n'est retabli que trech ms avant la prochaine étincelle, condition indispensable
  //pour une bobine à faible resistance, disons inférieure à 3 ohms.Typiquement trech = 3ms.
  Timer1.attachInterrupt(isr_GestionIbob);//IT d'overflow de Timer1 (16 bits)
  Timer1.initialize(Dsecu);//Le courant dans la bobine est coupé si aucune etincelle durant Dsecu µs
  Mot_OFF = 1;
  digitalWrite(Bob1, 0);//par principe, couper la bobine
  digitalWrite(Bob2, 0);//par principe, couper la bobine
}
void  isr_GestionIbob()////////////////////while (1); delay(1000);/////////////////////////////
{ Timer1.stop();    //Arreter le decompte du timer
  if (UneEtin == 1){
  digitalWrite(Bob1, 1);  //Retablire le courant dans bobine
  digitalWrite(Bob2, 1);  //Retablire le courant dans bobine
  }
  else
  { digitalWrite(Bob1, 0);//Preserver la bobine, couper le courant
    digitalWrite(Bob2, 0);//Preserver la bobine, couper le courant
    Mot_OFF = 1;//Permettra à loop() de detecter le premier front de capteur
  }
  UneEtin = 0;  //Remet  le detecteur d'étincelle à 0
  Timer1.initialize(Dsecu);//Au cas où le moteur s'arrete, couper la bobine apres Dsecu µs
}

void Prep_courbe()////////////////////////
{
  N1  = 0; Ang1 = 0; //Toute courbe part de  0
  int i = 0;    //locale mais valable hors du FOR
  pN++; pA++; //sauter le premier element de tableau, toujours =0
  for (i  = 1; *pN != 0; i++)//i pour les C1,C2 et Tc.Arret quand regime=0.
  //pN est une adresse (pointeur) qui pointe au tableau N.Le contenu pointé est *pN
  { N2 = *pN; Ang2 = *pA;//recopier les valeurs pointées dans N2 et Ang2
    k = float(Ang2 - Ang1) / float(N2  - N1);
    C1[i] = float(AngleCapteur - Avancestatique - Ang1 + k * N1) / float(AngleCibles);
    C2[i] = -  float(NT * k) / float(AngleCibles);
    Tc[i] = float(NT / N2);
    N1 = N2; Ang1 = Ang2; //fin de ce segment, début du suivant
    pN++; pA++;   //Pointer à l'element suivant de chaque tableau
  }
  j_lim = i - 1; //Revenir au dernier couple entré
  Tlim  = Tc[j_lim]; //Ligne rouge
}

void Change_de_Courbe()///////////////////

{ // Avec a,b ou c on change de courbe, sinon delta de +1 deg à +6 deg  ou negatif 11 à 16
  while (BT.available() > 0) //Nb de car dans le buffer venant du sphone
  { carLu = BT.read(); //oui il y a un car au moins
    //Serial.println(carLu);
    
  }
  if (carLu != "") //Une valeur a été entrée au sphone
  {
    
  if ((carLu=='a')||(carLu=='b')||(carLu=='c')||(carLu=='d')||(carLu=='e')){
  Select_Courbe_sphone();  //Ajuster éventuellement les pointeurs pN et pA pour la courbe b ou c 
  Prep_courbe();
  }
  if ((carLu=='f')||(carLu=='g')||(carLu=='h')||(carLu=='i')||(carLu=='j')){
  Select_Courbe_dep_sphone();
  }
  
  else {
    
  }
  }
}

void  Select_Courbe()////////////while (1); delay(1000);/////////////////////////////
//Par défaut, la courbe a est déja selectionnée
{ valPot1 = analogRead(Pot1);
  Serial.print("Le selecteur 1 = "); Serial.print(valPot1); Serial.print(" ,Centrifuge = ");
  if (valPot1 < 99)  {                  // Shunt 0 ohm donne 15 
    Serial.println(", Courbe a");
  }
  if (valPot1 > 110 && valPot1 < 150) { // Résistance de 4K7 donne 130 
    pN = &Nb[0];  // pointer à la courbe b
    pA = &Angb[0];
    Serial.println(" Courbe b");
  }
  if (valPot1 > 320 && valPot1 < 360) {  // Résistance de 18K donne 340    
    pN = &Nc[0];  // pointer à la courbe c
    pA = &Angc[0];
    Serial.println(" Courbe c");
  }
  if (valPot1 > 545 && valPot1 < 585) {  // Résistance de 47K donne 565    
    pN = &Nd[0];  // pointer à la courbe d
    pA = &Angd[0];
    Serial.println(" Courbe d");
  }
  if (valPot1 > 715 && valPot1 < 755) {  // Résistance de 100K donne 735    
    pN = &Ne[0];  // pointer à la courbe e
    pA = &Ange[0];
    Serial.println(" Courbe e");
  }
  if (valPot1 > 995) {                  // Pas de shunt donne 1015 
    Serial.println(" Courbe a");
  }
}

void  Select_Courbe_depression()////////////while (1); delay(1000);/////////////////////////////
// tableau des valeurs mmHg vs 8 bits
// {0,707}{25,667}{50,620}{60,601}{75,576}{80,565}{95,538}{100,530}{125,485}{150,438}{175,394}{185,373}{200,350}{210,330}{225,305}{250,260}{275,216}{300,172}
{ valPot2 = analogRead(Pot2);
  Serial.print("Le selecteur 2 = "); Serial.print(valPot2); Serial.print(" ,Depression = ");
  if (valPot2 < 99) {                  // Shunt 0 ohm donne 15 
    xhigh = 330; // soit 210 mmHg
    xlow = 565;  // soit 80 mmHg
    yhigh = 300; // soit 30°
    ylow = 0;    // soit 0°
    Serial.println(" Courbe a");
  }
  if (valPot2 > 110 && valPot2 < 150) { // Résistance de 4K7 donne 130 
    xhigh = 330; // soit 210 mmHg
    xlow = 538;  // soit 95 mmHg
    yhigh = 280; // soit 28°
    ylow = 0;    // soit 0°
    Serial.println(" Courbe b");
  }
  if (valPot2 > 320 && valPot2 < 360) {  // Résistance de 18K donne 340    
    xhigh = 350; // soit 200 mmHg
    xlow = 601;  // soit 60 mmHg
    yhigh = 320; // soit 32°
    ylow = 0;    // soit 0°
    Serial.println(" Courbe c");
  }
  if (valPot2 > 545 && valPot2 < 585) {  // Résistance de 47K donne 565    
    xhigh = 350; // soit 200 mmHg
    xlow = 538;  // soit 95 mmHg
    yhigh = 320; // soit 32°
    ylow = 0;    // soit 0°
    Serial.println(" Courbe d");
  }
  if (valPot2 > 715 && valPot2 < 755) {  // Résistance de 100K donne 735    
    xhigh = 305; // soit 210 mmHg pour essai 225 mmhg
    xlow = 538;  // soit 60 mmHg pour essai 95 mmhg
    yhigh = 280; // soit 28° 28° pour essai 24B
    ylow = 0;    // soit 0°
    Serial.println(" Courbe e");
  }
  if (valPot2 > 995) {                  // Pas de shunt donne 1015 
    xhigh = 330; // soit 210 mmHg = 330
    xlow = 565;  // soit 80 mmHg = 565
    yhigh = 300; // soit 30°
    ylow = 0;    // soit 0°
    Serial.println(" Courbe a");
  }
}
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
void loop()   /////////////////////while (1); delay(1000);/////////////////
////////////////////////////////////////////////////////////////////////////
{ 

   demoBTsmartphone();
}
////////////////DEBUGGING////////////////////////
//Voir les macros ps ()à et pc() en début de listing

//Une autre possibilité est de générer ou non du code de debug à la compilation.
//#define DEBUG    // #if defined DEBUG #endif

//Hertz = Nt/mn / 30 , pour moteur 4 cylindre
//N 1000,1500,2000,2500,3000,3500,4000,4500,5000,5500,6000,6500,7000,7500,8000,8500,9000,9500,10000
//Hz  33, 50,   66,  83  100  117   133 150   166 183 200    216  233 250   266 283   300 316 333

//Hertz = Nt/mn / 60 , pour moteur 2 cylindre
//N 1000,1500,2000,2500,3000,3500,4000,4500,5000,5500,6000,6500,7000,7500,8000,8500,9000,9500,10000
//Hz  16,  25,  33,  41   50   58   66   75   83   91  100  108  116  125  133  141  150  158   166
//Capteur Honeywell 1GT101DC,contient un aimant sur le coté,type non saturé, sortie haute à vide,
//et basse avec une cible en métal. Il faut  CapteurOn = 0, declenche sur front descendant.
//Le capteur à fourche SR 17-J6 contient un aimant en face,type saturé, sortie basse à vide,
//et haute avec une cible métallique. Il faut  CapteurOn = 1, declenche sur front montant.

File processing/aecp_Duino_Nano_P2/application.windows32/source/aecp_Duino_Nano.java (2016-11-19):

import processing.core.*; 
import processing.data.*; 
import processing.event.*; 
import processing.opengl.*; 

import g4p_controls.*; 
import processing.serial.*; 

import java.util.HashMap; 
import java.util.ArrayList; 
import java.io.File; 
import java.io.BufferedReader; 
import java.io.PrintWriter; 
import java.io.InputStream; 
import java.io.OutputStream; 
import java.io.IOException; 

public class aecp_Duino_Nano extends PApplet {

// Need G4P library

// On importe la librairie qui permet de communiquer en s\u00e9rie


Serial myPort; // On cr\u00e9\u00e9 une instance de la classe Serial
short LF = 10; // "Fin de ligne"

char HEADERSPEED = 'S'; // C'est le caract\u00e8re que l'on a ins\u00e9r\u00e9 avant la valeur de vitesse

int speedValue; // Une variable pour stocker la valeur de vitesse
float pressionValue; // Une variable qui stocke le nombre de degr\u00e9 de d\u00e9pression
int pressionadcValue; // Une variable qui stocke la valeur brute de conversion ADC du capteur
int mmhgValue; // Pour convertir pressionadcValue en mm de mercure mmHg
String spressionValue;
int delayValue; // Une variable pour stocker la valeur du d\u00e9lai
int delaydegValue; // Une variable pour stocker la valeur du d\u00e9lai d'un degr\u00e9
float errordelay; // Une variable pour stocker la valeur d'erreur du d\u00e9lai
float correctederrordelay; // Corrig\u00e9 pour anihiler l'action de la d\u00e9pression dans le calcul de l'erreur
float errordelaypercent;

int topSignal = 90; // Une variable pour stocker la position du capteur
int NT = 60000000; // NT = 120000000/nombre de cylindres
int Ncyl = 360; // Ncyl = 720/nombre de cylindres 360\u00b0 pour 2 et 180\u00b0 pour 4 cylindres , temps entre 2 tops
int dwellandcodetime = 0;
int dwellandcodetime2 = 0;
float usPerDegree;
float delayDegree;
float advanceStatic;
float correcteddelayDegree;
String scorrecteddelayDegree;
float delayAvanceDegree;
String sdelayAvanceDegree;
float delaySpark;
String sdelaySpark;
int indexCurve; // Pour s\u00e9lectionner une courbe allumeur
String nameCurve; // Le nom de la courbes
String titleCurve; // Le titre du graphique
String titleCurve2;// deuxi\u00e8me ligne de titre du graphique

PImage img;
PImage img2;

PFont ft;
PFont ft2;
PFont ft3;
PFont fg;
PFont fg2;
PFont fg3;
PFont fe;
PFont fe2;
PFont fe3;
PFont f;
String[] advanceCurve = new String[176];
String[] depressionCurve = new String[16];
int[][] mydepressionx = new int[12][1];
int[][] mydepressiony = new int[12][1]; 

int myspeedRaw;
float[] myspeed = new float[176];
float mydepressionRaw;
float[] mydepression = new float[300];

int q;
int xcentOrigin = 390;
int xdepOrigin = 960;
int ycentOrigin = 650;
int ydepOrigin = 650;
Boolean stateCent = true;


Table table;

Boolean stateCheck1 = true;
Boolean stateCheck2 = false;
Boolean stateCheck3 = false;
Boolean stateCheck4 = false;
String stringList = "Dyna Z";
String stringList2;
String stringList3;
String stringList4;
String stringList5;
String stringName = "Types mines";
String stringName1;
String stringName2;
String stringName3;
String stringName4;

int time;
int day;int month;int year;
int hour;int minute;int second;
int timestart;
int timestop;
int elapsedtime;
int elapsedtimesec;
int elapsedtimemsec;
Boolean stateCheckbtnrun = true;
Boolean stateCheckbtnrunfree = true;
Boolean stateCheckbtnpause = true;
Boolean stateCheck5 = true;
Boolean stateCheck6 = false;
String stringrpmmin;
int Irpmmin;
Boolean rpmmin = false;
int runrpmmin = 0;
Boolean Brpmmin = true;
String stringrpmmax;
int Irpmmax;
Boolean rpmmax = false;
int runrpmmax = 0;
Boolean Brpmmax = true;

float[] myrpmy = new float[1241];
float[] mycenty = new float[1241];
float[] mydepy = new float[1241];

int xrpmPos = 0;         // variable abscisse  - x
float yrpmPos=0;  // variable yPos - ordonn\u00e9e
int xcentPos = 0;         // variable abscisse  - x
float ycentPos=0;  // variable yPos - ordonn\u00e9e
int xdepPos = 0;         // variable abscisse  - x
float ydepPos=0;  // variable yPos - ordonn\u00e9e
int xrorpm = 40; // Origin x du cardre de l'historique rpm voir coordonn\u00e9e du cadre dans gui.pde
int yrorpm = 330; // Origin y du cardre de l'historique rpm voir coordonn\u00e9e du cadre dans gui.pde
int xrocent = 40; // Origin x du cardre de l'historique cent voir coordonn\u00e9e du cadre dans gui.pde
int yrocent = 500; // Origin y du cardre de l'historique cent voir coordonn\u00e9e du cadre dans gui.pde
int xrodep = 40; // Origin x du cardre de l'historique dep voir coordonn\u00e9e du cadre dans gui.pde
int yrodep = 650; // Origin y du cardre de l'historique dep voir coordonn\u00e9e du cadre dans gui.pde

String sName = "mesure";
String sExportdata;
String[] sData = new String[1241];

Boolean stateCheckbtnsave = true;
Boolean stateCheckbtnload = true;

Plot p;  //Globals
Aef aef;
String cFN = "Aecp.conf";
StringDict config;

float[][] records1 = new float [1241][3];
float[][] records2 = new float [1241][3];
float[][] records3 = new float [1241][3];
float[][] records4 = new float [1241][3];
float[] yrsave = new float[1241];
float[] ycsave = new float[1241];
float[] ydsave = new float[1241];

Boolean stateC1 = false;Boolean stateC2 = false;Boolean stateC3 = false;Boolean stateC4 = false;
Boolean stateC5 = false;Boolean stateC6 = false;Boolean stateC7 = false;
int oraC = color(245,110,5); // orange
int blC = color(10,10,255); // bleu
int reC = color(255,10,10);// rouge
int veC = color(10,255,10); // vert
int jaC = color(252,252,41); // jaune
int orC = color(175,152,18); // or

public void setup(){
  size(1350, 690, JAVA2D);
  createGUI();
  customGUI();
  // Place your setup code here
  smooth();
  // A vous de trouver quel port s\u00e9rie est utilis\u00e9 \u00e0 l'aide de print(Serial.list())
 String portName = Serial.list()[32];
 //print(Serial.list());
 // On initialise la communication s\u00e9rie, \u00e0 la m\u00eame vitesse qu'Arduino
 myPort = new Serial(this, portName, 115200);
 
 myPort.bufferUntil('\n');
 
 // Make a new instance of the file dataCurve for loading some data

 nameCurve = ("a4114a.txt");
 advanceCurve = loadStrings(nameCurve);
 depressionCurve = loadStrings("depressionCurve.txt");
 

 
 
 // Make a new instance of a PImage by loading an image file
  img = loadImage("panhard242.png");                // Using a String for a file name
  
 // Loading a font for displaying text for title
  ft = loadFont("Courier10PitchBT-Bold-32.vlw"); 
 
 // Loading a font for displaying text for title
  fg = loadFont("Courier-Bold-18.vlw"); 
 
 // Loading a font for displaying text for title
  fe = loadFont("Courier-Bold-12.vlw"); 
   
 // Loading a font for displaying text 
  f = loadFont("Courier-Bold-22.vlw"); 
  
  aef = new Aef();
  p = new Plot();
  config = new StringDict();
  loadConfig(cFN);  //Path to the config file should be "argv" or so !

  for (int q = 0; q<175; q++){
    myspeed [q] = 0; // initialise le tableau d'avance centrifuge pour \u00e9liminer les "scories" !!!
  }
}
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

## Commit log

2015-01-27 First commit to create project
    [Vérification formule pour Arduino.ods, aecp.brd, aecp.kicad_pcb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]
2015-03-26 New version of software & source-code for hardware
    [tableauaideselection.csv]
2016-07-02 New update with an Arduino Nano_V3 as board , 2016 project
    [Vérification formule pour Arduino Nano aecp.ods, Vérification formule pour Arduino.ods, aecp.brd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]
2016-07-02 New schematic
2016-07-03 Add new picture of the board
2016-07-04 New version of source code for Processing & Arduino
2016-07-06 Add new schématic and new board under Kicad, also a new version under Arduino
    [aecp_Nano_V2.kicad_pcb, aecp_Nano_V2.sch]
2016-07-07 A bug with a picture of the new board corrected
2016-07-08 Add new version of source code for Processing & Arduino
2016-07-09 New version of aecp under processing with the motor M10S
2016-07-10 Add new version of source code with the type of motor
2016-07-10 Bug between M10S & M8S corrected
    [aecp_Duino_Nano.pde, aecp_duino_dep_Nano_M5_M6_M8_M10.ino, aecp_duino_dep_Nano_M8S.ino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]
2016-07-17 Add new version of Arduino's code
2016-10-16 New version of the PCB
    [aecp_Nano_V2.kicad_pcb, aecp_Nano_V3.kicad_pcb, aecp_Nano_V3.sch]
2016-10-22 New PCB version
    [aecp_Nano_V3.kicad_pcb, aecp_Nano_V3.sch]
2016-10-25 Last version of PCB with gerber files
    [aecp_Nano_V3_hall_sensor-B.Cu.gbr, aecp_Nano_V3_hall_sensor-B.Mask.gbr, aecp_Nano_V3_hall_sensor-B.SilkS.gbr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]
2016-11-18 Bug corrected in the PCB
    [aecp_Nano_V3-B.Cu.gbr, aecp_Nano_V3-B.Mask.gbr, aecp_Nano_V3-B.SilkS.gbr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]
2016-11-19 Add picture of the new PCB, soldering and mounting
2016-11-19 Bug corrected under processing
    [tableauaideselection.csv]
2016-11-25 New IHM under Processing 3.2.3
    [tableauaideselection.csv]
2016-12-25 New version of code under Arduino
2017-03-13 New version for Arduino and Processing 3.3 with bluetooth
2017-03-26 New source file for kicad with bluetooth adaptator
    [aecp_Nano_V3.kicad_pcb, aecp_Nano_V3.sch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]
2017-04-18 New version for Arduino and Processing
2017-07-09 Add new picture for the hardware and corrected source code for Arduino
    [aecp_duino_M5.ino, aecp_duino_M6_M8N.ino, aecp_duino_M8S.ino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]
2017-07-09 Add corrected source code for processing
    [tableauaideselection.csv]
2017-07-09 New version of android application and dummy for arduino
2025-07-23 Add new file with 2025 version called aecp_V4
    [aecp_Nano_V3_hall_sensor-B_Cu.gbr, aecp_Nano_V3_hall_sensor-B_Mask.gbr, aecp_Nano_V3_hall_sensor-B_Silkscreen.gbr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]
2025-08-31 Add manufacturing files of the complete 2025 version
    [Doigt AECP.step, Tete delco AECP V2.step, Tete delco AECP.step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]
